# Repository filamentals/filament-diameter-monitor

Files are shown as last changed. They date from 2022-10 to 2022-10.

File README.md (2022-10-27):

# Welcome to Filamentals!

### **Motivation:** 

FilaMentals is a project to develop an optical device to monitor the diameter of 3D-printer filaments that are produced by an extractor. Custom made extractors are susceptible to produce inhomogenous filaments which would not be useful for re-use in a 3D printer. So, the future aspiration of the project is to create a feedback loop between a FilaMental device and a filament extractor, such that the extractor parameters are automatically adjusted based on the FilaMental output and the desired filament diameter is achieved.  

### **Project Description:**

 A Raspberry Pi NoIR Camera (V2) is controlled by a Raspberry Pi 3 to monitor the filament. The camera and the filament are attached to a 3D-printed casing. The casing also involves a hole for a LED, which illuminates the filament. Later, the images of the filament are analyzed with the help of [OpenCV](https://opencv.org/) package to calculate the thickness. 

### **Build Status:** 

Currently, the project is at a prototpye phase. Data can be collected from filaments, although it cannot be attached to a extruder yet. The code is being optimized to execute faster and provide a better user interface.

### **Prototype image:**

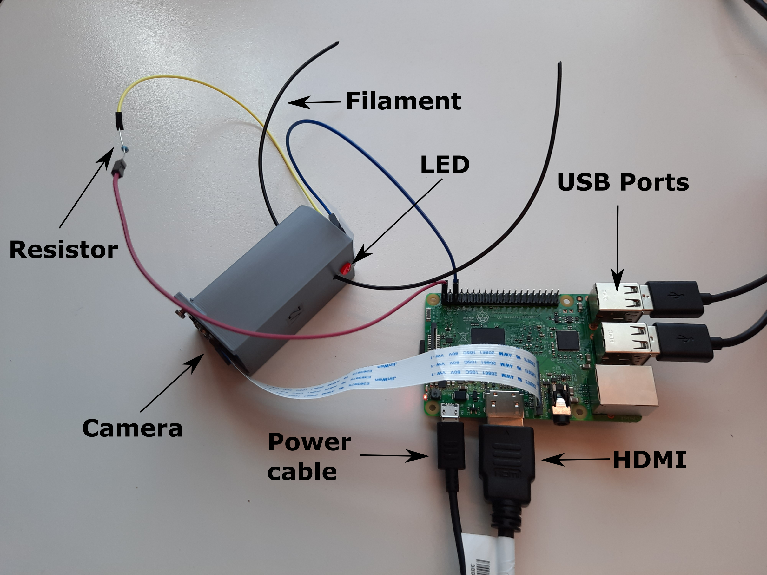
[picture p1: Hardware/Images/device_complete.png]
complete_device


The device has two parts: RaspberryPi (RasPi) and the imaging module. The former operates the device, while the latter contains the camera, filament hole, an LED and a resistor.

### **Installation:** 

For instructions to how to assemble the device click [here](Documentation/instructions/Installation.md).

### **Measurements:**

Currently this project gives live read-outs of filaments up to 5 mm of thickness. 

### **How to use:**

For the instructions of how to run the device click [here](Documentation/instructions/measurement_instructions.md)

### **Developers:**
     Ana Martins: @anaismartins
     Yoldas Cinemre: @YoldasCinemre
     Zach Meredith: @meredizp

### **License:**
For the license see [here](LICENSE).

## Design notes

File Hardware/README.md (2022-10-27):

In the *Hardware* folder the user will find these subfolders:
# Subfolders

1. [images](projects\Filamentals_Ana_Yoldas_Zach\Hardware\images) : photos about the hardware used
2. [stl_files](projects\Filamentals_Ana_Yoldas_Zach\Hardware\stl_files) : 3D models of the housing

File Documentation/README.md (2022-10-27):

In the *Documentation* folder the user will find subfolders and files:
# Subfolders

1. [feedback](projects\Filamentals_Ana_Yoldas_Zach\Documentation\feedback) : peer evaluations and feedback
2. [general_documentation](projects\Filamentals_Ana_Yoldas_Zach\Documentation\general_documentation) : contains logbook and timetable
3. [instructions](projects\Filamentals_Ana_Yoldas_Zach\Documentation\instructions) : contains installation and measurement instructions
4. [presentation](projects\Filamentals_Ana_Yoldas_Zach\Documentation\presentation) : contains pitch documentation and presentations given
5. [previous_pictures](projects\Filamentals_Ana_Yoldas_Zach\Documentation\previous_pictures) : contains photos taken by our prototype

# Files
1. [project_canvas](projects\Filamentals_Ana_Yoldas_Zach\Documentation\project_canvas_Ana_Yoldas_Zach.md) : our purpose, outcomes, and process

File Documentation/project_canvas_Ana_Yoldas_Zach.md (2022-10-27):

*Utrecht Experiment Design 2022*

# Project canvas

### POP

+ **Purpose**: to make the project requirements, boundaries, and goals as concrete as possible  
+ **Outcome(s)**: list your project steps, the best possible outcome, and the minimum desired outcome  
+ **Process**: self-reflection and discussion with your mentors

PROJECT NAME: Filamentals

TEAM: Ana Martins, Yoldaş Cinemre, Zach Meredith

# Project description  
Our main goal is to create a monitoring system for a filament extruder.
We wanted to start by following an Open Source project that consists of an optical sensor that measures the width of plastic filament in real time. From there, assuming we have the time, we want to extend to monitor other parameters, like density or extrusion rate.

*25/09/2022 Update*
- We are no longer following the open source project that uses the optical sensor, since the sensor array used in the project is no longer manufacuted.
- As a result we are now creating a method of optical measurement through the combination of a Raspberry Pi and a Pi Camera.
- The new method will need a redesinged camera mount and a way to attach the sensor to the extruder.
- We plan on using OpenCV algorithm for diamater detection of the filament.

### Open Hardware and its purpose
We started by looking at this project: https://www.sciencedirect.com/science/article/pii/S2468067218300208, which is the full filament extruder, and then looking closely at what they use for monitoring, we want to follow this open source project: https://www.thingiverse.com/thing:454584
We connect with the idea of recycling plastic and giving it a new life. Especially considering the current popularity of 3D printing, one of our ideas is to recycle failed prints or unused prints, so as to not generate so much waste.

### Potential users of the hardware and its added value
While producing the filament, it is important to know its properties, to make sure it is of high enough quality.
The potential users are the general public, since 3D printing is now so widespread. This will allow people to produce their own filament at a low cost value, while also recycling.
This can also be used for high end level prototyping, when considering extrusion rate and a time involved in 3D printing.

### Underlying physics and working principles
The first sensor we are planning on using is an optical sensor. From there, mainly thermodynamics will be involved.
The sensor directly monitors the filament being extruded and displays it in real-time.

### Required components and planned alteration to the reported recipe

*Required Components*:
- Raspberry Pi
- Pi Camera
- 3D Printed Casing
- OpenCV

Something we want to add is displaying a graph with the history of the monitored data, so that we can figure out the optimal set up for extruding. Comparing our filament with industry-produced would also be a goal.

### Chosen method of interfacing with a computer
Using a RaspberryPi, we want to create a feedback loop, where the system controlls itself when parameters are outside the acceptable values, and through this we will be able to start and stop the monitoring.

### Planned measurements
Diameter, moisture content, density, extrusion rate, elasticity, temperature.

## Mid-course review of your project state (fill this mid-course)
### Current status (24/10/22):
+ **Hardware:** Currently we have designs for 3D-printed casings that create a suitable environment for the imaging of filaments. The [installation](instructions/Installation.md) is shown to be easy, as tested by an independent group of users who had no prior experience with the set-up.
+ **Software:** We have a code that analyzes an image of the filament in the casing, and calculate the average thickness. The principles of how this works can be found [here](../Software/working_principles_summary.md).
+ **Interfacing:** The user can interact with the device by connecting the RaspberryPi to a monitor and running the code to access a graphical user interface. This interface contains a live readout of the measured diameter, as well as means to start, stop, calibrate the device. The output is then recorded in a seperate text file. Instructions to make measurements can be found [here](instructions/measurement_instructions.md).

### Deviations from the original plan:
+ We decided to restrict our measurements to filament diameters, as opposed to the initial plan to measure temperature, density, extrusion rate etc. Such goals are not within the capabilities of our current equipments and would require seperate designs of their own. We do not have the time to work on this in the timeframe allocated to the project.
+ Given the time restrictions, it is also improbable that we will manage to connect the device to a filament extruder and establish a feedback circuit. The next step for any future work on the project would be on this aspect. 

### Planned adjustments:
+ Currently, the device is not as robust as we want it to be. It seems that little changes in the positioning of filaments may cause the device to fail in making measurements. We aim to increase robustness by adding a diffuser in our design, so that the light will be more uniform. We think that this will make it easier for the device to recognize the edges of filaments.

### Updated Projects Description:
*(As written in the main README)*

FilaMentals is a project to develop an optical device to monitor the diameter of 3D-printer filaments that are produced by an extractor. Custom made extractors are susceptible to produce inhomogenous filaments which would not be useful for re-use in a 3D printer. So, the future aspiration of the project is to create a feedback loop between a FilaMental device and a filament extractor, such that the extractor parameters are automatically adjusted based on the FilaMental output and the desired filament diameter is achieved.  

 A Raspberry Pi NoIR Camera (V2) is controlled by a Raspberry Pi 3 to monitor the filament. The camera and the filament are attached to a 3D-printed casing. The casing also involves a hole for a LED, which illuminates the filament. Later, the images of the filament are analyzed with the help of [OpenCV](https://opencv.org/) package to calculate the thickness. 

## Final review of the project accomplishments (fill at the end of the course)

+ list the achievements of your project  
+ write down your plans for improving your project or making it more widely accessible

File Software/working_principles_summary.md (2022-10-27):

Here is a brief explanation of how the algorithm to analyze the images works.

First the camera takes a picture:
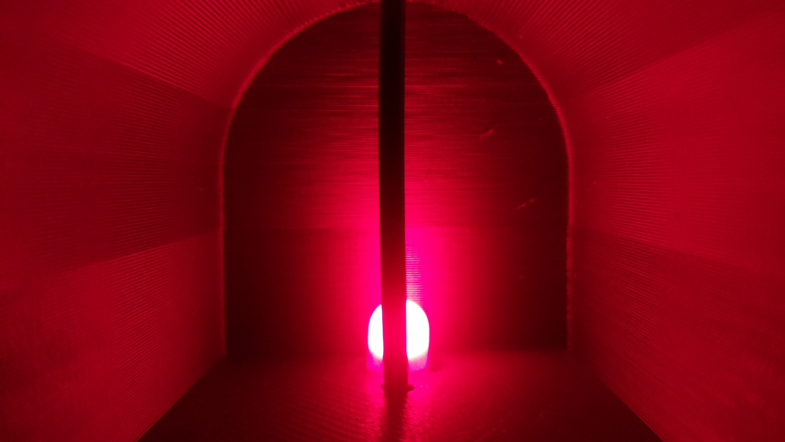
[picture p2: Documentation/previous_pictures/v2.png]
first_pic


Then it is cropped in the middle for analysis. This needed to ensure that the diameter is mostly consistent throughout the image and that it does not see the visual noise from the set-up: 

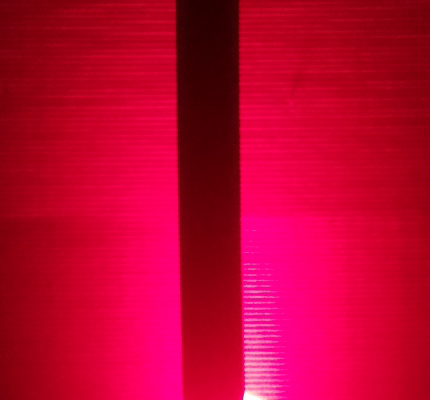
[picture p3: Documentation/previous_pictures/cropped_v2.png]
cropped


Later the code detects the edges in the image (see [here](code/edge_detection.py) for the code):

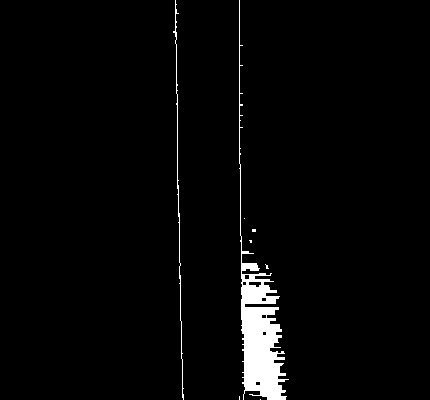
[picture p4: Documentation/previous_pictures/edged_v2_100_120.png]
edges


Then the edges of the filament are recognized as lines with the `HoughLines()` method (see [here](code/line_detection.py)). The code later seperates the image in the middle to classify the pixels belonging to each lines. Hence, it is important that the filament sits symmetrically in the middle of the image. Superimposed on the original image we can see the recognized lines (shown in blue):

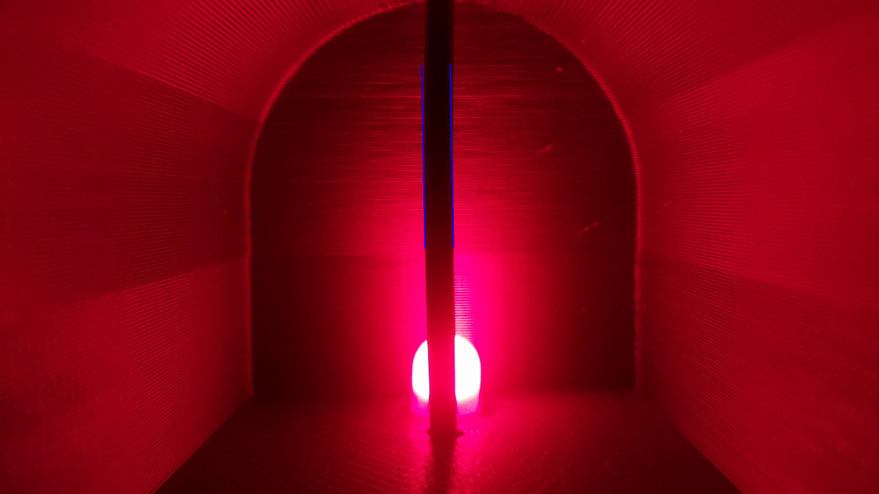
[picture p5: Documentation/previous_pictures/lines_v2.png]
lines


Finally the thickness is [calculated](code/distance_calculator.py) by taking the distance between points on the lines and averaging them. The final results are then exhibited on the interface.

**Note:** The code for the edge detection is tuned for the spesific brightness provided by the LED in the current design. If the equipment is altered, so should the code. By changing the `min_threshold` and `max_threshold` values in the [code](code/main.py), the user should find the optimal value for their set up such that the majority of the noise is filtered out and the filament edges can be detected.

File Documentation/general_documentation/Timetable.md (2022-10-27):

# FilaMental's Timetable 

**Preface**: For scheduling we are using an [online calendar](https://calendar.google.com/calendar/embed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) to plan and keep track of free time slots of the group.

## Week of September 25th:
- [X] Update Raspberry Pi OS
- [X] Connect PiCamera
- [X] Collect first image
- [X] Determine lens range
- [X] Decide if we'll use current camera case
  - Won't use the current one --> need to make a new one due to the fact that camera should be covered from external light. See [logbook](LogBook.md#300922-friday-first-use-of-opencv).
- [X] Get familiar with Python and OpenCV

 ## Week of October 2nd:
- [X] Design base for stabilizing the filament
- [X] Design method of attachment to either a printer or extruder
- [X] Test run with OpenCV in factory produced filament (known diameter)
- [ ] Update README.md with documentation for using the experiment

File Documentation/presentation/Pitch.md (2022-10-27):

# Pitch #
## Video Idea 1
1. [ ] Plastic in water
2. [ ] Pick up plastic
3. [ ] Cut to Filamentals Logo
4. [ ] Proto Lab
5. [ ] Using extruder and it's protblems
6. [ ] Goal of our project
7. [ ] Our prototypes and community involvement
8. [ ] Future of the project

## Video Idea 2
1. [X] Someone drinking from a bottle
2. [ ] Throws bottle away but slaps out of hand and put in shreeeeder
3. [ ] Cut to Filamentals Logo
4. [ ] Close up of Extruder
5. [ ] Close up of housing
6. [ ] Our growth plans (video of us working on project)
7. [ ] Reaching out to community

## Pitch narration
It is no secret that our world is drowning in plastic. These products that made our lives easy have long been unchecked. But no more! If we have the power to create plastic, we also have the power to re-shape it!

Since the dawn of time, humanity had the unresistible urge to shape the world around them. They built their civilization with the skills to mould materials, but in the process left the mother nature in peril. But no more! For if humanity can bend even the hardest metal to their will, they have the power to shape the destiny of their plastic trash. 

In the recent years, people have developed ways to re-use plastic. By putting them through steel and fire in an extruder, we can now reshape plastic in the form of filaments to be used in 3D-printers or other utilitarian purposes. However, unsupervised power yields no prosperity but only chaos. FilaMentals is a open-hardware project to create a low-cost monitoring system for the diameter of these filaments. Using a Raspberry Pi, camera, an LED and a 3D-printed casing, a FilaMental device gives a live reading of the filament diameter. The simplicity of the design allows it to be used in any custom made filament extruder. 

The future is bright, but it's surely brighter with FilaMentals in it. Our outlook involves establishing a feedback loop with the filament extruder, allowing automatic control of the machine to make filaments with thicknesses desired by the user. Thanks to this ease of use, we hope more people will be motivated to start extruding themselves and help with the global effort to battle plastic waste!

**Outro:** FilaMentals! "insert motto"

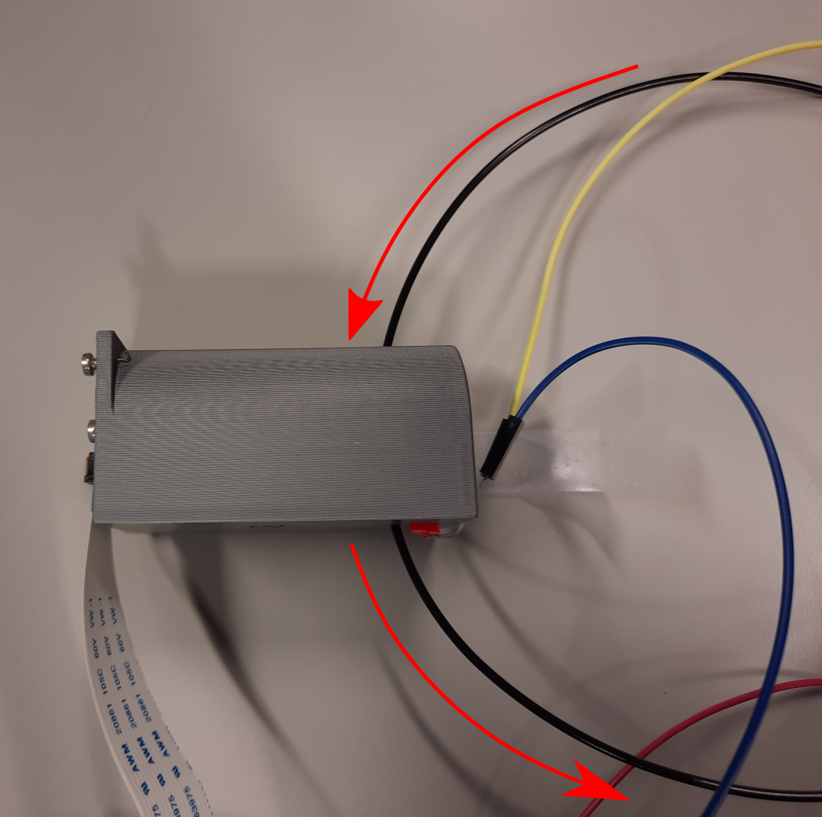
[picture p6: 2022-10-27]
Hardware/Images/filament_insertion.png

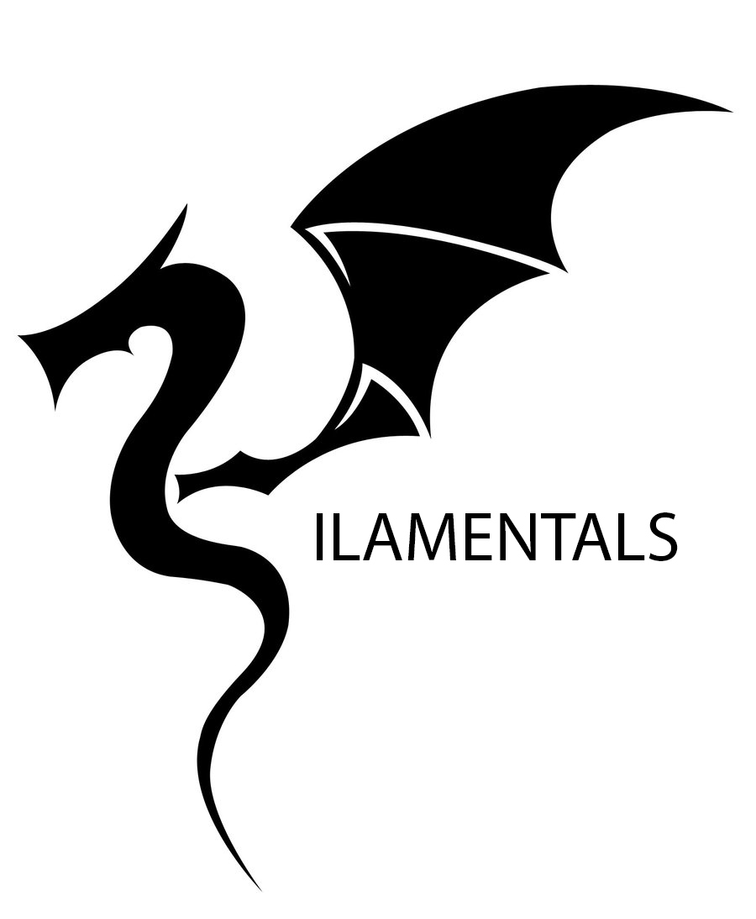
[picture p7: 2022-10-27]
Documentation/presentation/Filamentals v1.png

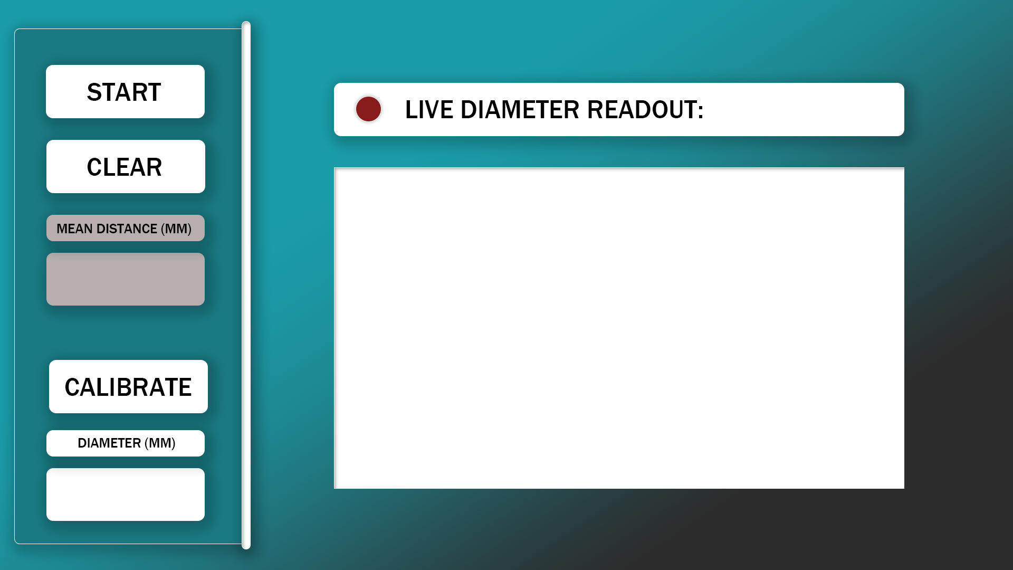
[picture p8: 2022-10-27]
Software/gui_mockup/FilaMentals_GUI.png

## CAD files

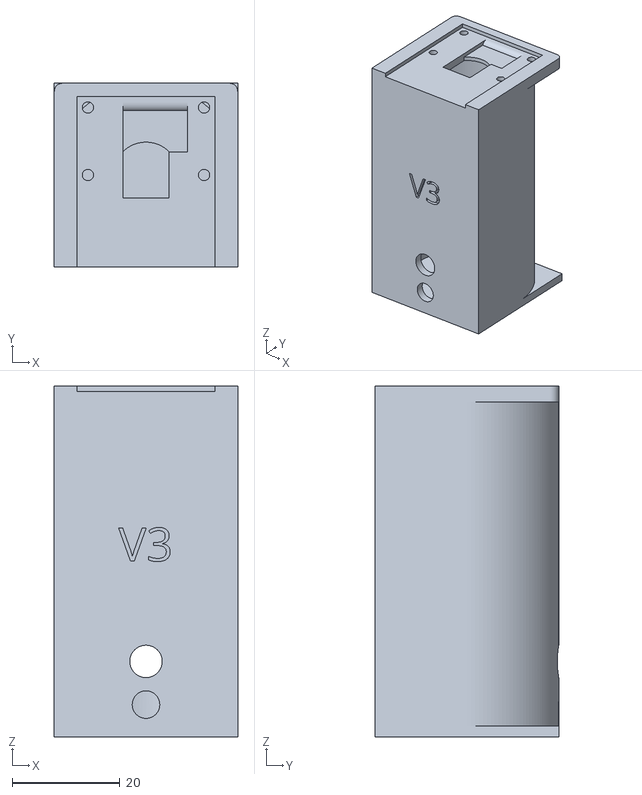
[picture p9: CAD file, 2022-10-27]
Hardware/stl_files/filament_observer_v3_chamfer.stl
34.0 x 34.0 x 65.0

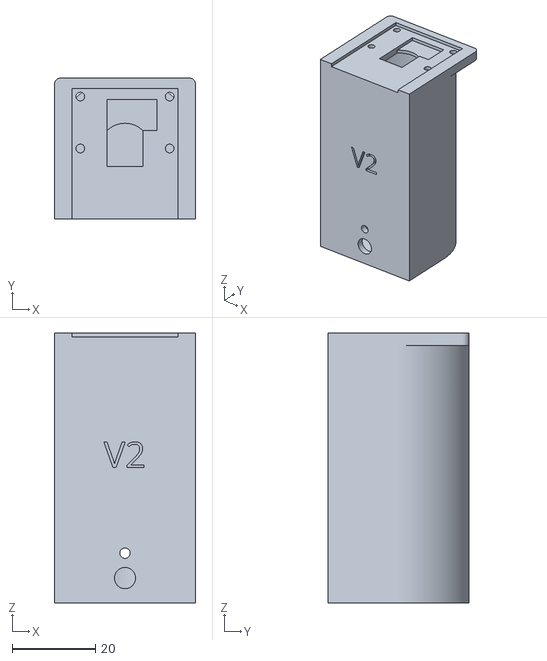
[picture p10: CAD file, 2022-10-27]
Hardware/stl_files/filament_observer_v2.stl
34.0 x 34.0 x 65.0

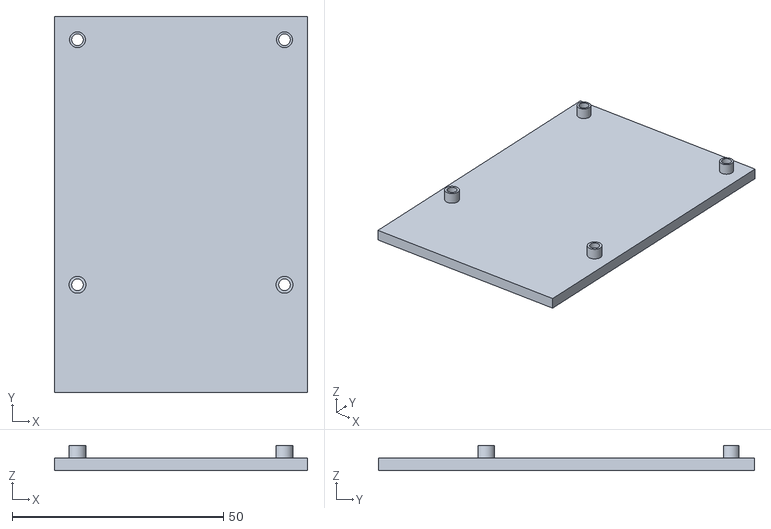
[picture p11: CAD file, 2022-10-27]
Hardware/stl_files/rpi_base_v1.stl
60.0 x 89.0 x 6.00

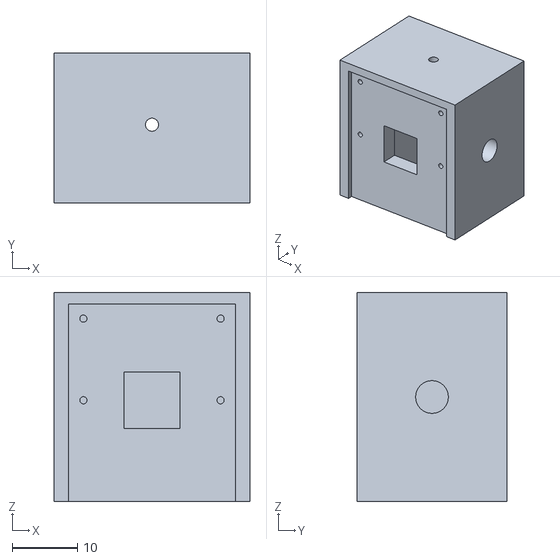
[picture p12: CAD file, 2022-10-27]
Hardware/stl_files/filament_observer_v1_LED.stl
30.0 x 23.0 x 32.0

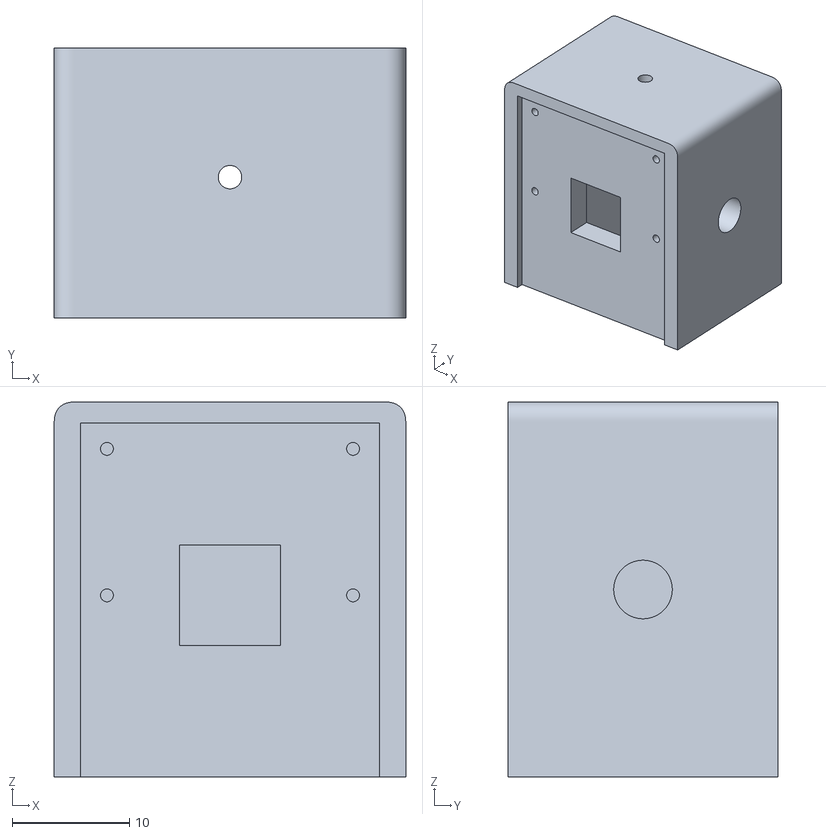
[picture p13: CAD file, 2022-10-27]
Hardware/stl_files/filament_observer_v1_LED_chamfer.stl
30.0 x 23.0 x 32.0

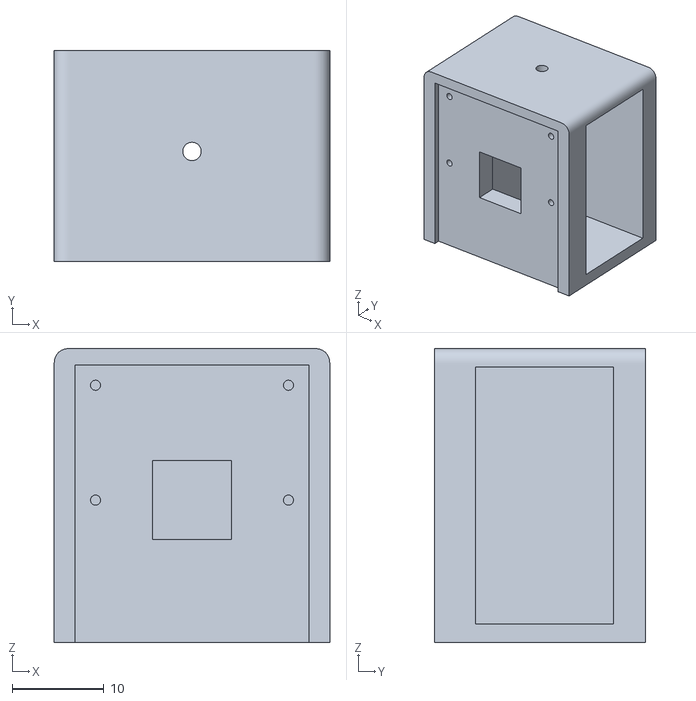
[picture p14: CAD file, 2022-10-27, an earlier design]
Hardware/stl_files/filament_observer_v1.stl
30.0 x 23.0 x 32.0

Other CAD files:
Hardware/stl_files/filament_observer_v2_chamfer.stl

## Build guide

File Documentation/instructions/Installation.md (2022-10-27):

# **Assembling the Device** 
## **Parts list:**
+ [Raspberry Pi 3 Model B](https://www.raspberrypi.com/products/raspberry-pi-3-model-b/)
+ [Raspbery Pi NoIR Camera V2](https://www.raspberrypi.com/products/pi-noir-camera-v2/)
+ Red LED, 5 mm diameter
+ Resistor, 150 Ohm
+ Female-female cables (x3)
+ [3D-printed casing](../../Hardware/stl_files/filament_observer_v2_chamfer.stl).
+ [3D-printed Raspberry Pi mount](../Hardware/SLT_Files/RPi%20Base%20V1.stl) (optional to mount on Raspberry Pi)
+ HDMI cable
+ Ethernet cable
+ Keyboard, mouse, and monitor (for interfacing)
+ USB-micro cable (power supply)
+ M2.5 mm screws (x4)
+ M2.6 mm screws (x4)(optional to mount on Raspberry Pi)

## **Hardware Assembly:** 
+ Take the M2.5 mm screws and mount the camera on to the 3D-printed casing
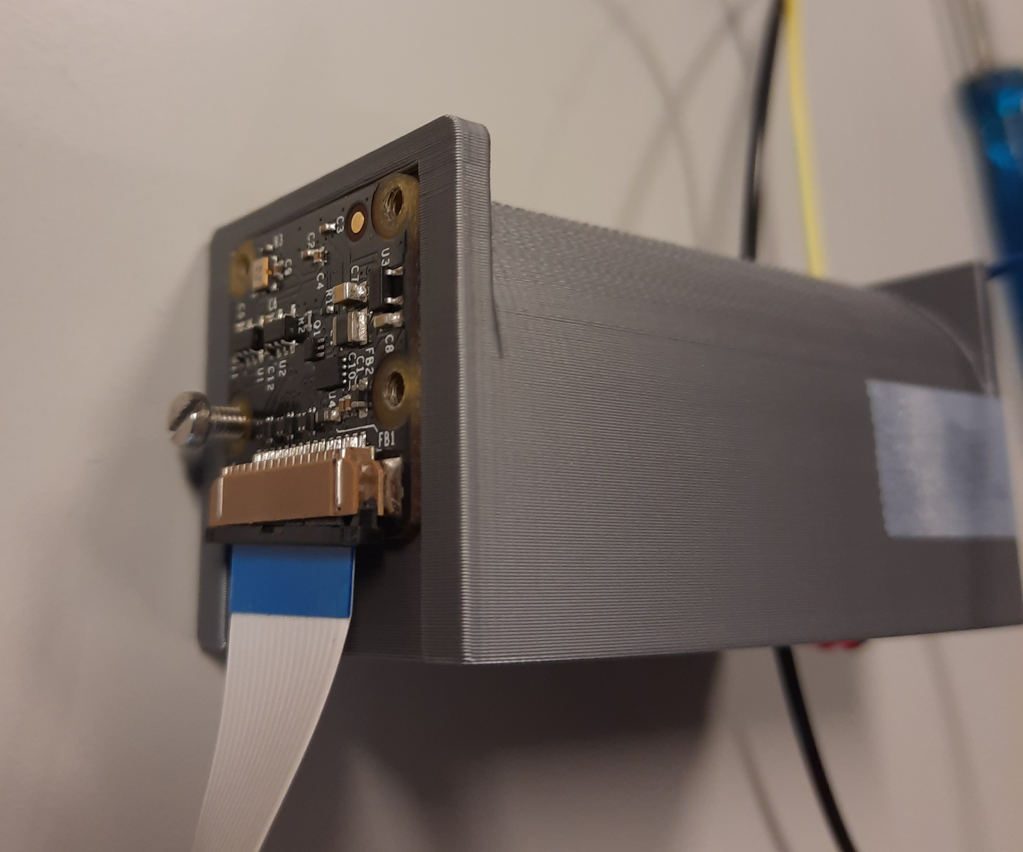
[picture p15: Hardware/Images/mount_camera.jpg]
camera_mount
  + 
+ [Connect the camera into the Raspberry Pi](https://www.techcoil.com/blog/connect-raspberry-pi-camera-module-raspberry-pi-2-raspberry-pi-3/). :warning: If you connect it while the RaspberryPi is running, the camera will break down. **Always make sure that the camera is connected to the RasPi before powering it**. :warning:
+ Connect the LED and the resistor via a female-female cable (make sure you use the longer leg of the LED). Then connect the other legs of the resistor and the LED to the Raspberry Pi as shown below:

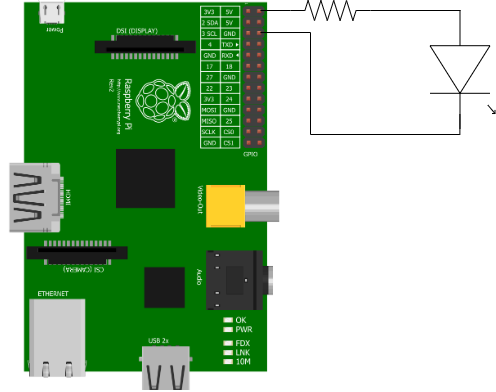
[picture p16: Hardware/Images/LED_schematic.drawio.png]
wirig_diagram
  
  **Note:** The LED and the resistor determine the brightness inside the 3D-printed casing. It is important to use the exact materials since the software is tuned accordingly. If you wish to use different materials, you would need to change some parameters in the code for it to recognize the filament. See the [summary of working principles](../../Software/working_principles_summary.md) for more information. 
+ Insert the LED in the 5 mm hole of the 3D-printed casing. 
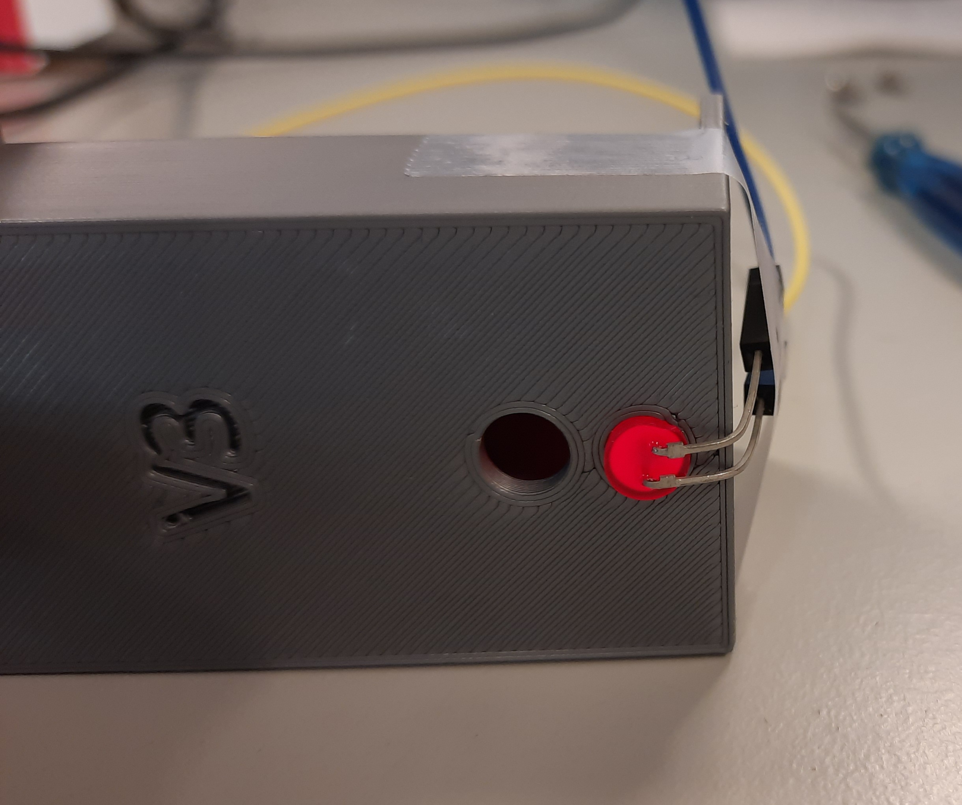
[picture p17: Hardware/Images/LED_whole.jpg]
LED_insert
  + 
+ Connect the Raspberry Pi to: 
  + the mouse and keyboard through USB ports,
  + the monitor with an HDMI cable,
  + the internet through an ethernet cable.  
  
  See the overview [image](../README.md) again, if you wish to check where the ports are on the Raspberry Pi.
+ :warning: Make sure again that the camera is connected to the Raspberry Pi :warning:.
+ Connect the power cord to the RaspberryPi. You will see a red light at the corner of the RasPi, indicating that it is powered on. The LED should also turn on at this point, if it is set up properly.

## **Software Installation:**

Once you manage to access and control the RaspberryPi through the monitor, you should follow these steps to install the required software into the RaspberryPi. If you have already done this, locate [here](measurement_instructions.md) to find the instructions to make measurements.

+ [Install the operating system](https://raspberrytips.com/install-raspbian-raspberry-pi/)
+ [Initialize the camera](https://projects.raspberrypi.org/en/projects/getting-started-with-picamera)
+ Check that the camera is connected by running the command:
  + `vcgencmd get_camera` 
  + This should give the output:
  + `supported = 1, connected = 1` 
+ Install `git` by running the commands
  + `sudo apt-get update`
  + `sudo apt-get install git`
+ Check if Python is installed by running the command
  + `python --version`
+ The version used in this project is 3.9.2. If you do not have is installed, [install it](https://handtoolsforfun.com/how-to-install-python-3-on-a-raspberry-pi-3/).
+ Clone the project repository with `git clone https://git.science.uu.nl/ued2022/ued2022.git`
+ Locate to the folder by using `cd ../ued2022/projects/Filamentals_Ana_Yoldas_Zach/Software/code` and run the command  `pip install -r requirements.txt` to install the libraries required for the code. 

**Next:** The system is ready to insert the filament and [make measurements](measurement_instructions.md!

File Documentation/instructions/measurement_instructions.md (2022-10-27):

# **Making measurements:**

The filament you wish to measure should be pushed through the two holes on the 3D-printed casing. It is most probable that the filament will be curved because of its elastic properties. To make the device work correctly, position the filament as shown below. 

filament_insertion

This will ensure that the filament sits symmetrically in the middle of the images. To understand why this is required, see the [summary of working principles](../../Software/working_principles_summary.md) of the code. 

Since the casing is a prototype and not designed to be attached a filament extruder, you will need to move the filament by hand.

Now, locate to the code folder in the project repository using: 

`cd Desktop/ued2020/projects/Filamentals_Ana_Yoldas_Zach/Software/code`

and run:

`python gui.py`

A graph will appear with the y-axis showing the thickness measurements while the x-axis shows the timesteps. You can also see the  buttons to start/stop, calibrate, and clear measurements.

## How to calibrate 
The device has a default calibration using an industrial 3D-printer filament with a diameter of 1.75 mm. However, it can be calibrated with another filament. To do that:

1. Insert a filament in the 3D-casing whose diameter you know.
2. Run the program, and let it run for at least 10 cycles. 
3. Insert the real diameter of the filament on the top right and click on "Calibrate".
4. Now you are ready to measure other filaments.

## Test measurement
Now let us make a measurement to check that the calibration is done well.

1. Insert the piece of calibration filament by paying attention to its curvature as instructed before. 
2. Start the program. The measurements will begin immediately, but you can stop and start it any time with the buttons.
3. After each measurement that appears in the graph, pull the filament slightly by hand to analyze a different segment.
4. The interface should calculate 1.75 mm for the thickness. Congratulations! The calibration is confirmed.
5. Now the device is ready to be used with other filaments.
## Possible errors
+ The terminal might show `Edges not found`. This indicates that the code failed to recognize the filament edges and/or distinguish them. When this happens, the measurement is ignored and it's not registered in the interfacial graph. **Possible Solutions:**
  + Adjust the filament as instructed above such that it's positioned symmetrically in the middle of the image (see [here](../Software/WorkingPrinciples_summary.md) to read more about why it is important.) 
  + It might also be that the filament is deformed in that region. Pull the filament a little bit to measure a different segment.
  + If the problem persists, investigate the edge detection seen by the camera. The symmetry and uniformity of the filament can be visualized here. This can be done by locating the stored photos taken by the camera. These photos can be found under [Software > output](../software/output/) and are labeled by their set min/max threshold. Select the file with the current threshold values. The current version is:
    + Min Threshold: 100
    + Max Threshold: 120
  
     *Thus the file name is as follows: edged_pic_100_120.png*
## Notes
+ For a summary of the working principles of the algorithm see [here](../Software/WorkingPrinciples_summary.md)

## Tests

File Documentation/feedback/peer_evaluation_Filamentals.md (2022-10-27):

# Reproducibility report

## Experiment/team: 
Filamentals by Ana Martins (@1760068), Yoldas Cinemre (@64795611) and Zach Meredith (@1069713)

## Reviewers: 
Riya Banerjee (@5073014) and Carlo van Maaren (@6835791)

## Report 

### Documentation:

1. **Could you understand the purpose of the experiment? Explain.**  
> Yes, this was very clear from the start as the README file in the main directory runs you through the motivation for the project and the project description.

2. **Were the safety instructions clear?**
> There were warning messages for the code and the setup (e.g. having to make sure that the camera is connected to the RaspberryPi before powering it), as well as a “Possible errors” section, but there was no true safety instructions which in our opinion also is not truly required since the project is very safe.

3. **Was the starting point and the expected duration of the measurements clear in the documentation?**  
> The starting point was easy to find because the main README file contained links to the documents in which the setup, calibration and measurement instructions were explained. The duration of the actual measurement or an estimate thereof, however, was not documented, but the GUI conveniently shows when the program settles to a particular filament diameter. For the calibration, it is said to run the program for 10 cycles, however we feel the number of cycles is not clearly indicated (the x-label of the graph in the GUI is labeled "timesteps").

4. **Does the documentation contain all necessary information to successfully reproduce the measurement? If not, what was missing?**
> We think the documentation mostly contains all the necessary information, perhaps having some extra README files in each subfolder would be helpful to better navigate through the project. 

5. **Did you get stuck at some point? What extra help did you need to proceed?**
> Initially, we got stuck trying to install all the required programs on our laptops which resulted in a few bugs we had to resolve (i.e. “from main import main errors” and having some problems installing picamera on Windows). After discussing with the project team, we figured out that we could simply use the desktop that was already connected to the device and from there everything went smoothly.

6. **Are you encouraged to reproduce previous measurements? How easily could you navigate through the project documentation?**
> The measurements we reproduced were the calibration and test measurement, after which we tried the extruded filament and a few cables to test the device. The calibration and test measurement were well-explained and we were encouraged to actually perform them in the documentation. 
Navigating through the project documentation was clear, but we do have a few pointers which will be given below (7).

7. **What can be improved in the documentation?**
> We like the use of the PIP install via the requirements file, but it is only described in the installation file. It would be useful if this was also mentioned in the software folder. For our purposes, however, it was fine since we did not have to install anything ourselves. 
To continue, the gui.py file is now located in the code folder (within the software folder) but there is also a “gui” folder in which there are only an image and a psd-file of the graphical user interface. We could imagine that people would look into the gui folder for the Python code as well, so perhaps renaming that folder to “GUI_images” or something similar would be better. You could also [convert your Python program to an executable file](https://www.geeksforgeeks.org/convert-python-script-to-exe-file/) and place that in the folder (while also having the actual code in the “code” folder). 
In addition, we would advise you to make the “Documentation” folder more structured by the use of subfolders, similar to those in the hard- and software folders.
Finally, as stated, we would use README files in the subfolders as well so that the reader is guided better through your documentation. This would also resolve some of the improvements mentioned above.

**On the scale of 1-5 (1: top quality, 5: disappointing) how do you assess the documentation? Please justify your grade based on the questions above.**

#### Documentation grade: <mark>**2**</mark>

### Measurements:

1. **Can you operate the setup with the provided instructions?**
> Once we figured out that we had to connect the power cable and use the desktop that was already connected, operating the setup was rather easy because of the graphical user interface. The provided instructions were clear and sufficient, but – as mentioned in the documentation – the software returned “Edges not found” a lot, especially when using the extruded filament. We will go more into some ideas we have  to resolve this in the following.

2. **How close were the results you obtain to the previously reported results?** 
> The calibration and test measurements were spot on. The measurements we performed after that were also pretty close (± 0.1 mm).

3. **Is the analysis procedure easy to understand? Summarize it briefly in your own words.**
> The analysis is done by the software itself. Its function is described in a working principles summary which was a very nice addition. This procedure we now want to describe in our own words.
The camera makes an image of the interior of the device in which the filament is placed. Behind the filament there is a LED which illuminates the interior of the chamber, so that the camera can capture the silhouette of the filament. This image is then cropped so that the variation in filament diameter will not influence the analysis. After that, you use a set of OpenCV functions to find the edges of the filament cross section (`cv2.canny`). Next, you use the `Houghlines()` method from OpenCV to recognize the edges as lines and compute the distance between the two. This should then give the diameter of the filament. 

4. **Is the setup robust and safe to operate?** 
> Yes, it mostly is. We would suggest making a holder for the RaspberryPi and all the electronics since they seem somewhat fragile.

5. **Did you encounter any issues? Could you troubleshoot those issues without contacting the owners?**  
> Once we have figured that we had to use the desktop that was already connected to the RaspberryPi, we only encountered issues in the form of the “Edges not found” warning which, as stated, was already mentioned in the documentation. Sometimes by adjusting the filament (which is something you also give as a possible solution), the warning went away, but most of time this was not the case. After discussing with a member of the project team we came to the conclusion that we should just accept this for the current standing of the project.

6. **What part of the measurement procedure did you appreciate most?**  
> We think the GUI is a very nice touch as this makes the experience for the user a lot nicer. Though not technically part of the measurement, we would also like to comment that getting an insight into the working principles of the algorithm was also a highlight of the reproducibility exercise.

**On the scale of 1-5 (1: top quality, 5: disappointing) how do you assess the measurements reproducibility? Please justify your grade based on the questions above.**

#### Reproducibility grade: <mark>**1.5**</mark>

### Interactions:

1. **If you had to perform work on this part of the project, would you have selected the same goal or aimed at something else? Please, explain.**  
> Initially we thought that you were going to actually build a full filament extruder from which we personally would not have immediately thought of making a filament sensor. After the presentation it became clear that there was already a filament extruder in Lili’s Proto Lab. From here, it indeed seems logical to look into improving this device instead and a filament sensor is a step we also could have taken from there. 

2. **Which instructions did you need from the owners on top of the written files?**  
> As beforementioned, the only thing we really needed was the pointer that we had to work on the desktop that was already connected to the device. We were initially starting to download the required libraries and trying to get the code working, but in the end all of that was already done for us! Thank you, team Filamentals!

3. **Does the experiment accomplish its stated purpose?**
> It does. We were able to determine the diameter of several filaments and wires. 

4. **What do you recommend to the project owners to improve their complete package?**

> _Documentation_

We think most of the project documentation is clearly ordered and complete. That being said, we do have a few tips (some of which are already discussed above):
1.	Add README files to the subfolders as well. This way you know where to find what in the subfolder. For example, when we looked for the gui.py file, we initially were looking in the “gui” folder, assuming the graphical user interface might be located in a separate folder. Something to add here, is that you could look into converting the GUI to an executable file and only place that file in the “gui” folder while keeping the actual code in the “code” folder ([conversion instructions](https://www.geeksforgeeks.org/convert-python-script-to-exe-file/)).
2.	Installing the required libraries via a single PIP install (through the requirements file) is a very good addition. For now it is only described in the installation file, however. We think it would be useful if this was also mentioned in the software folder. 
3.	We would advise you to make the “Documentation” folder more structured by the use of subfolders, similar to those in the hard- and software folders.

> _Measurements_

The measurements were very easy to perform because of the graphical interface. This is really nicely done! The graph shown in the GUI had a x-label “timesteps”. We wondered whether those actually refer to the number of cycles or an actual measure of time. In the former case, we would advise you to alter the calibration instructions so that they match. Otherwise, in the latter case, we would advise you to also include the number of cycles / elements that were used for the averaging so that you do not have to keep track of that yourself. You could also inform the user that the calibration (and with that the 10 cycles) are done.

> _Hardware (bonus)_

Since you guys did so well in the documentation and measurement side of the project, we also wanted to include some ideas we had on fixing some of the issues that you are still trying to solve (e.g. hopefully get rid of the “Edges not found” warnings). 
1.	To start, we noticed that the LED results in a flair in the images which in turn causes the OpenCV modules to recognize different edges than the ones of the actual filament. This could maybe be resolved by using a dim (homogeneous) back light which covers the entire back wall (i.e. the wall which is captured by the camera), or by making a ‘hallway’ for the LED (to reduce difference in radial distance from the light source) and using a diffusive plastic sheet (to dim the LED – might not be necessary anymore after including the hallway). This way the entire background will be illuminated in the same manner and contrast will be improved. In the images we clearly see the print lines which result in unwanted analysis results. By removing the back wall and replacing it with something non-3D printed (i.e. the back light), these lines will no longer be present and the OpenCV detection will most likely function a lot better. Furthermore, due to the light being a lot dimmer, the flairs should not be there anymore. If you manage to find a multi-color back light, you will also be able to adjust the color to have maximum contrast with the filament. 
2.	To tie in on this, we would also suggest painting the side walls of the chamber in black so that more of the indirect light is absorbed. This way the filament will only be illuminated from the back and print lines in the side walls will not cause lines in the images which could be recognized by the OpenCV modules. 
3.	Furthermore, you could look into using adjustable rollers on either side of the filament entrance and exit holes as this would make the feeding a lot more consistent, with less bending of the filament. By making them adjustable you are still able to use different filament gauges.
4.	As stated, we would also like to suggest making an enclosure for the wiring to improve the robustness of the device.
5.	In some talks we had about your project, you mentioned that you were also in the process of speeding-up the code. We think you will find a way to do this, but we also want to give you a different option that involves more of the hardware side. We encountered [this YouTube video]( https://www.youtube.com/watch?v=RYgdLPe_T0c) which describes a cheap solutions that requires much less computational power and analysis. Perhaps you can combine the two mechanisms and write an algorithm that uses the pre-estimated diameter to more quickly find the filament diameter through the optical path.
6.	Finally, we came across [this article](https://www.researchgate.net/publication/346555509_Open_Source_3-D_Filament_Diameter_Sensor_for_Recycling_Winding_and_Additive_Manufacturing_Machines) in which a multi-axes measurement is described using mirrors. This would give you a better indication of the actual shape of the filament, thereby making it a much better sensor than the 1D alternatives. If you guys have time, it would be awesome if you could also implement this!   

______

### Response to reviewers

_This part must be filled by the project owners based on the peer feedback_

1. **Which major adjustments did you make based on this feedback?**
 1. [ ] We are planning to redesign our lighting system to try to elimintate the "no edge found" error.
- [X] Design a diffuser slot
- [X] Design more reflective (homogenous) background
 2. [X] We plan on changing the x-label in our live graph from timesteps to cycles.
 3. [ ] We will design a more robust housing and consider the touch screen for the Raspberry Pi.
 4. [ ] We will further explain the calibration principle to clarify future confusion.
 5. [X] We will output the diameter of the filament
 6. [X] We will implement a red = recording
 7. [ ] We will upload our project details to JOGL.
 8. [ ] We will write down our clear goals, how far we plan to get, and the following steps of our project.
 9. [X] Update project canvas.
 10. [ ] We will clarify that the Raspbery Pi is a desktop and only needs a monitor and keyboard to use, not a separate laptop.
 11. [ ] We will clarify the link why making diameter measurements correlates to recycling plastic.
 12. [ ] We will try and record information aobut how long each measurement takes.
 13. [ ] We will look into the theoretical background of this project.
 14. [ ] We will clean up and reorganize our subfolders to adapt to the knowledge of each individual user.
- [X] Rename image folder to GUI images
- [X] More sub-folders in Documentation
- [X] README in each sub-folder with description of that sub-folder

2. **Do you agree with the graded assessment of the reviewer?**
In the context of this course, our team believes that our documentation is clear and precise enough to be considered a 1.5 over the 2 that we were originally scored.

**On the scale of 1-5 (1: really helpful, 5: disappointing) how do you assess the peer evaluation? Please explain.**
1.5: We believe that the feedback given was very descriptiive and near a perfect response. We were given, not just the problems of our project, but also possible solutions to overcome these problems. The only negative we found was that some of the advice was a little unhelpful simply due to them not being possible for integration to rasberry pi. Feedback is good, only when it applies to the project.

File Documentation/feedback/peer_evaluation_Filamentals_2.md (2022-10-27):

# Reproducibility report

## Experiment/team: 
[Filamentals](projects/Filamentals_Ana_Yoldas_Zach) by Ana Martins (@1760068), Yoldas Cinemre (@64795611) and Zach Meredith (@1069713)

## Reviewers: 
Uma Lau (@5127416)

## Report 

### Documentation:

1. **Could you understand the purpose of the experiment? Explain.
> In the part of Open Hardware and its purpose, there are links for people to look in detail of the background for the project and the used open hardware, which is desirable. However, I do think it would be better if there are more explanations of project purpose or a summarized description. The contents about the experiment purpose in both README and project canvas is a bit sketchy for now, which merely mention the custom-made extractors are insusceptible to produce a re-useable homogeneous filament in 3D printer. Indeed, this allows me to know the reason of building a monitoring system for filament extruder; whereas, without introducing why extractors fail to produce such a filament, how the extractors work and look like, and etc., it would be hard for me to obtain a deeper understanding of how much the monitoring system improve the facility. Also, there seems have a jump in the explanation of the aim, for instances, I am a bit confused on how this device aid to the recycling of the failed prints or unused prints. Doing measurements are not filling the gap of that.     

2. **Were the safety instructions clear? 
> Yes, the safety instructions are clear. There are warning symbols around the bolded safety remarks, which are placed in the right place and with appropriate amount.

3. **Was the starting point and the expected duration of the measurements clear in the documentation?  
> Despite the duration of the measurements is not shown, there is clear and readable instruction on performing the measurement. I can follow them easily. 

4. **Does the documentation contain all necessary information to successfully reproduce the measurement? If not, what was missing? 
> I found it is a bit difficult to push the material into the casing. During this process, the material is damaged a little bit and it is also stuck in the halfway. If this will affect the measurement result in some way (because the diameter might be slightly different) or disturbing the imaging (because there might be some crumbs left inside the casing after various measurements), I think this should be mentioned in the documentation.     

5. **Did you get stuck at some point? What extra help did you need to proceed?
> Everything is stated and labelled, that is good! I can follow every step on the hardware building. The steps for software installation are also listed in a good order with useful links and grey highlights. The code is not that difficult to comprehend.       

6. **Are you encouraged to reproduce previous measurements? How easily could you navigate through the project documentation?  
> Yes, there is not much error sources for the results of the measurement. If you can follow every step listed in the page and take care of the possible (procedural) errors, the results are quite stable. Meanwhile, the project documentation navigation is managed very well because each step is clearly stated. Both hardware and software components used are quite handy to construct. 

7. **What can be improved in the documentation?  
> Still, I hope there will be more explanations in the part of [working principles] ( projects/Filamentals_Ana_Yoldas_Zach/Software/WorkingPrinciples_summary.md) or the theoretical background. Also, if the pictures are adjusted in a smaller size and with some descriptions below, that would be nicer.   

On the scale of 1-5 (1: top quality, 5: disappointing) how do you assess the documentation? Please justify your grade based on the questions above.

#### Documentation grade: <mark>**2**</mark>

### Measurements:

1. **Can you operate the setup with the provided instructions? 
> Yes. Thanks for the labelling, that’s helpful and handy. 

2. **How close were the results you obtain to the previously reported results? 
> The resolution and shape of material edge obtained is quite like the provided results. Probably there is few millimeter’s differences, but that is omittable and within the acceptable range.  

3. **Is the analysis procedure easy to understand? Summarize it briefly in your own words.  
> All analysis of the measurement is done in the computer program. The graphical interface can calculate the thickness for us. We only need to compare the results. It is easy to handle.  

4. **Is the setup robust and safe to operate? 
> Yes, the setup is robust and safe and the caution about the power is also stated clearly. One thing is the thickness of material seems not fit the hole of the casing very well, maybe it is good to either make the hole larger or produce the thickness of material smaller.   

5. **Did you encounter any issues? Could you troubleshoot those issues without contacting the owners?
> No, everything is done smoothly. For troubleshooting, there is enough help from the part of possible errors.

6. **What part of the measurement procedure did you appreciate most?  
> I appreciate the part of test measurement; they are clear and simple.  

On the scale of 1-5 (1: top quality, 5: disappointing) how do you assess the measurements reproducibility? Please justify your grade based on the questions above.

#### Reproducibility grade: <mark>**1.5**</mark>

### Interactions:

1. **If you had to perform work on this part of the project, would you have selected the same goal or aimed at something else? Please, explain. 
> As mentioned above, I am not fully understanding the purpose of this project. I also think the measurement on the thickness is the main thing of this device, but if I could realize in a deeper way of its function, I would probably aim on other things.   

2. **Which instructions did you need from the owners on top of the written files?  
> The written files are well and sufficient.

3. **Does the experiment accomplish its stated purpose? 
> Yes, its measure the thickness as expected.

4. **What do you recommend to the project owners to improve their complete package?  
> I think add a README files to every subfolders would be better. Another thing is I feel the measurement maybe a bit simple. I recommend adding more type of measurements. 

______

### Response to reviewers

_This part must be filled by the project owners based on the peer feedback_

1. Which major adjustments did you make based on this feedback?  
2. Do you agree with the graded assessment of the reviewer?  

On the scale of 1-5 (1: really helpful, 5: disappointing) how do you assess the peer evaluation? Please explain.

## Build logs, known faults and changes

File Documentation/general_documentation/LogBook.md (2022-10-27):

# Welcome to the LogBook of our progress

Here the user can find notes on each step taken in the development of the project.

## 26/09/2022, Monday
+ Initial attempt to make pi camera work. 
+ :warning: DO NOT turn on RaspberryPi before attaching the camera. Always plug everything out, attach the camera and then plug the cords in to turn on RasPi. Otherwise, you will blow the camera. :warning:

## 29/09/2022, Thursday
### Instructions on how to connect the pi camera and taking a picture
+ Plug the camera in the RasPi. 
  + (instructions on how to open the holder, put the cord in and locking it, maybe with pictures)
+ Plug all the other necessary components to turn on RasPi. These are:
    + Mouse and keyboard
    +  Monitor
    +  Powercord
    +  **Note**: When the camera is attached, it takes the RasPi longer to turn on. If it takes too long, plug out the power and put it in again.
 +  You will see the screen of the RasPi on the monitor. Using the icon on the top, open a terminal. 
    + Use the command: `vcgencmd get_camera` to check that the camera is connected. If it is, you will get the output: `supported = 1, connected = 1`.
    + To take a picture use the command: `raspstill -o ~/Desktop/image.jpg`
    + **Note:** If the camera is out of focus, you can gently move the camera lens (counter-) clockwise to adjust the focus. 

## 30/09/22, Friday, First use of OpenCV
Yesterday the [first image](first-pic.jpg) was taken. The goal of this session is to use OpenCV to analyze the image and get a measure of the filament's thickness. Following sources are to be studied and used:
+ [Ordering coordinates clockwise with Python and OpenCV](https://pyimagesearch.com/2016/03/21/ordering-coordinates-clockwise-with-python-and-opencv/)
+ [Measuring size of objects in an image with OpenCV](https://pyimagesearch.com/2016/03/28/measuring-size-of-objects-in-an-image-with-opencv/)

Using the [code](../Software/code/edge_detection.py) to detect the edges of the filament we get [this](../Software/output/edged_first.png) kind of images. **Notes on the image:**
+ It seems that the lightning of the image is important for edge detection. It can be seen that the bright section on the top of the filament is detected as two lines. We need to avoid bright reflections off the surface of the filament. 
  + **Proposed solution**: We should aim to make a casing covering the camera, with a fixed light illuminating the sample. This would eliminate the light source as a random variable, increasing the reproducability. 
  + [ ] **Task**: Think about and ask for a small light source that might work for this purpose. Can the red LEDs we have would be useful?  

## 01/10/22, Saturday
**Today's goals**:
+ [ ] Achieving recognition of the top and bottom lines of the filament by the code
+ [ ] Figuring out the required distance between the filament and the camera such that the edges of it is not blurred.
+ [ ] Installing OpenCV in RasPi.
  + Apparently Python 10.2 crashed our OS... Reinstalling for next time. 
+ [X] Delving more into the tools of OpenCV.
  + It seems that the method used [here](https://pyimagesearch.com/2016/03/28/measuring-size-of-objects-in-an-image-with-opencv/) might not be applicable in our case, because that code requires the complete object to be in the image. It works by recognizing the object, drawing a rectangular contour around it and then taking the corners. In our images the filament will span across the whole image, hence the code might not recognize it as one object.  

## 02/10/2022 Sunday
**Today's goals**
+ [X] Reinstalling Pi OS (try the newest version since we knew that the camera was the issue the first time)
+ [X] Reinstall Python on Pi
  + We actually ended up leaving the Python that already came with Bullseye (Python 3.9) in fear of breaking it again. If there's any conflicts between our computers and the Pi, we'll downgrade in our computers. 
+ [X] Reinstall OpenCV
  + It worked first time...
+ [X] Reinstall GIT to simplify the process by coding on our computers
  + Already had the latest version installed! I can see the appeal in this new OS...
+ [X] Preliminary Camera Module Housing

## 03/10/22, Monday
+ [X] Go to the protolab and print the preliminary camera housing.
  + [This design](../Hardware/SLT_Files/FilamentObserver_w_LED_and_Chamfer_V1.stl) is being printed. 
+ [X] Get RGB LED
  + No need for it, red LED works pretty well already.
+ [X] Screw everything in the casing and take a picture
  + The picture is taken under the name pic_v1 
+ [X] Use edge detection software in the image
  + It seems that putting the light source at the side causes bright spots on one side, leading to a bad recognition of the edge on that side. 
  + **Proposed solution**: Put the light source at the side of one of the filament holes.
    + We did that by drilling a hole and the processing of the image leads to [this](../previous_pictures/edged_v140_100.png)
    + Now we get more clear lines detectable by eyes. Next step is to make it so that the computer also recognizes them as lines. 
  + New method to detect lines: [Houghline](https://www.geeksforgeeks.org/line-detection-python-opencv-houghline-method/)

## 07/10/22, Friday
**Summary of the progress since monday**:
+ We designed and printed V2 of the casing this time with a longer distance between the camera and the filament
  + Requires us to crop the image to analyze only the region around the middle of the filament, thus reducing unwanted edges that are recognized due to illumination of the sorrounding area.
  + Tried a white LED but it is too bright, causing unwanted edge detection --> stick to the red LED.
+ The [algorithm](../Software/code/edge_detection.py) to detect the edges of the filament as lines and measure the average distance (in pixels) between them works. 
  + There is variation however between initial measurements. We could see different measurements in pixels of the same, industrial filament
+ **Shortcomings for now**
  + In order to categorize which of the recognized lines belong to which edge of the filament, the code seperates the image in the middle. This poses a problem if the filament is positioned in such a way that it's curved. Then the code fails.
  + **Possible solutions:**
    + Design a casing such that the filament is strecthed, thus reducing the curvature.
    + Instruct the user to position the filament accordingly. 
  
### Progress today
+ Ana created the first version of the interface
  + Does temporal measurements (in pixels) and records them in a graph 
+ Yoldaş wrote more on the README
  + The skeleton seems to be ready to instruct the user to make a first measurement
  + [X] Images of the set up needs to be added
  + [X] Extra documents need to be created for further help if the user needs such as:
    + [X] How to connect another LED and changing the analysis parameters if the user uses other LEDs or resistors
    + [X] A summary of the working principles of the code (with images)

## 08/10/22, Saturday
+ Zach designed a nice interface.
+ Yoldaş put images of the set up in README and created the instructions of how to connect the LED and summary of the working principles.
+ Ana perfected the measurements and the interface.

## 10/10/22, Monday
**Goals:**
+ [X] Make the final presentable interface.
+ [X] Go over the doumentation and instructions to finalize them.

## 17/10/22, Monday
+ [X] Respond to the feedback.

## 20/10/22, Thursday
+ [ ] Make new casing with a hole for a light diffuser.
+ [ ]

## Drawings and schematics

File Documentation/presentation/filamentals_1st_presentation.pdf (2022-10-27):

01

# FilaMentals

ANA MARTINS
YOLDAŞ CINEMRE
ZACH MEREDITH

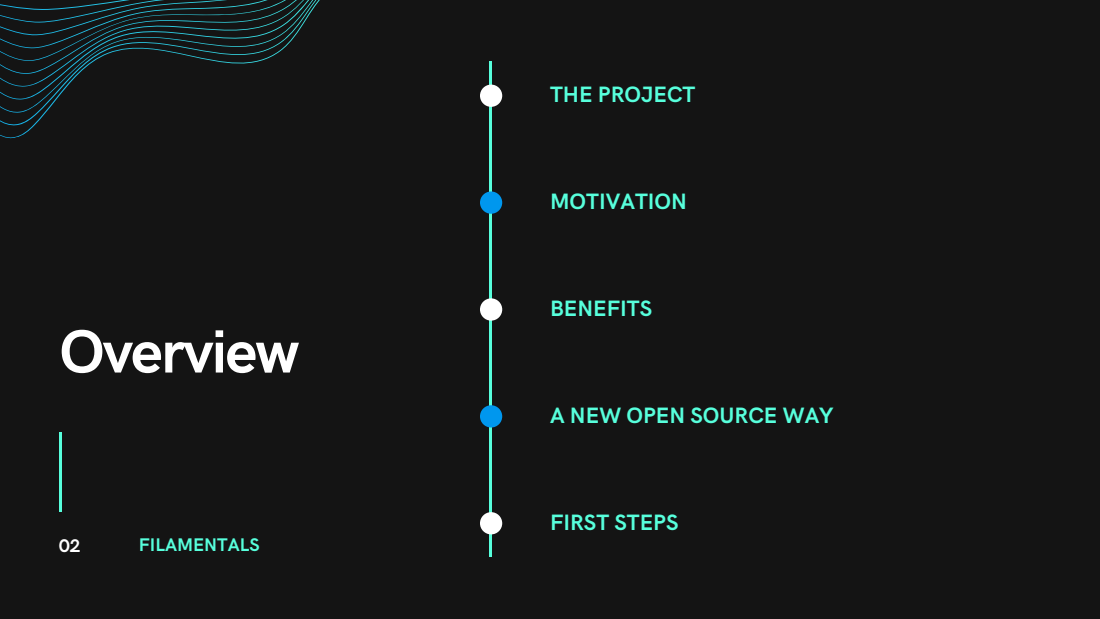
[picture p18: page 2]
Overview; THE PROJECT; MOTIVATION; BENEFITS; FIRST STEPS; 02 FILAMENTALS

A NEW OPEN SOURCE WAY

# The Project

## HOW WE GOT HERE

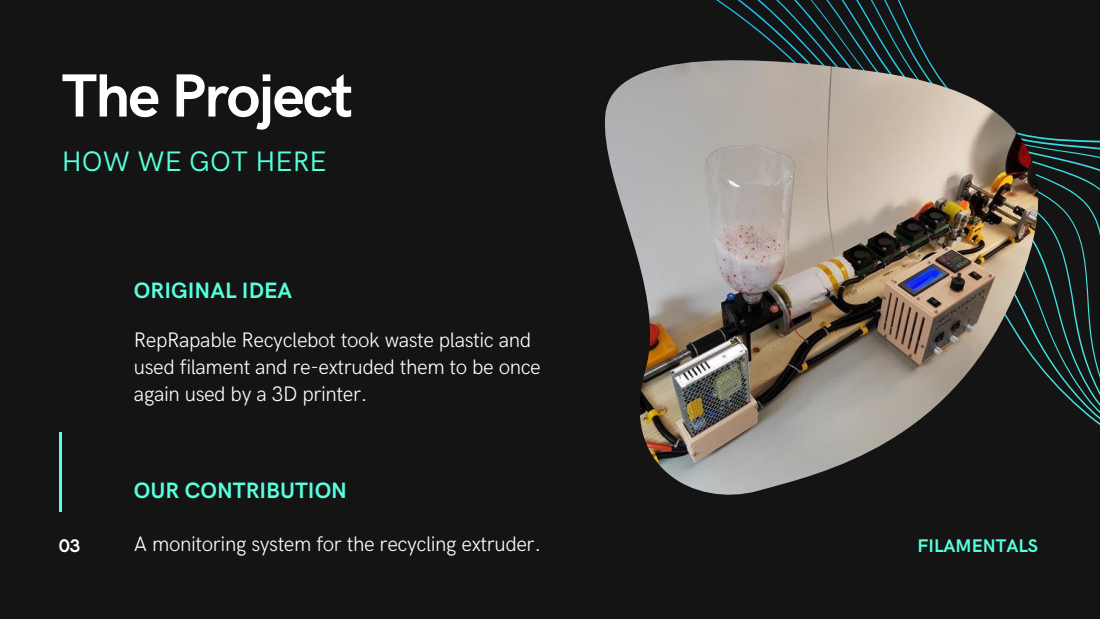
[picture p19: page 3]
ORIGINAL IDEA; OUR CONTRIBUTION; A monitoring system for the recycling extruder.; FILAMENTALS

RepRapable Recyclebot took waste plastic and
used filament and re-extruded them to be once
again used by a 3D printer.

# Motivation

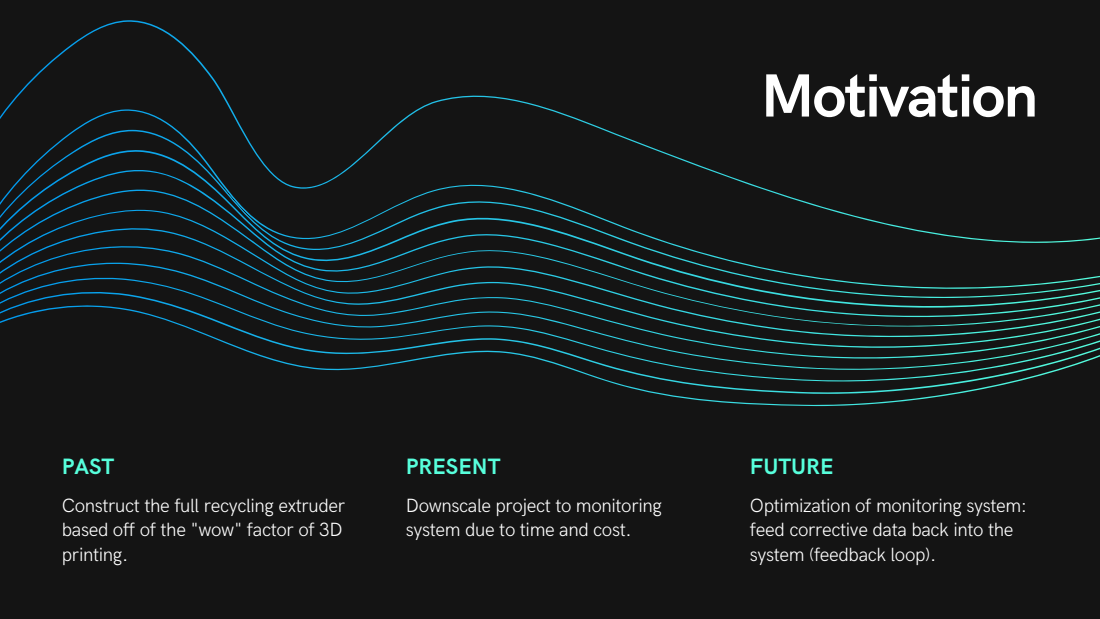
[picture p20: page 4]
wow; " factor of 3D

PAST
Construct the full recycling extruder
based off of the "
printing.

PRESENT
Downscale project to monitoring
system due to time and cost.

FUTURE
Optimization of monitoring system:
feed corrective data back into the
system (feedback loop).

# Benefits

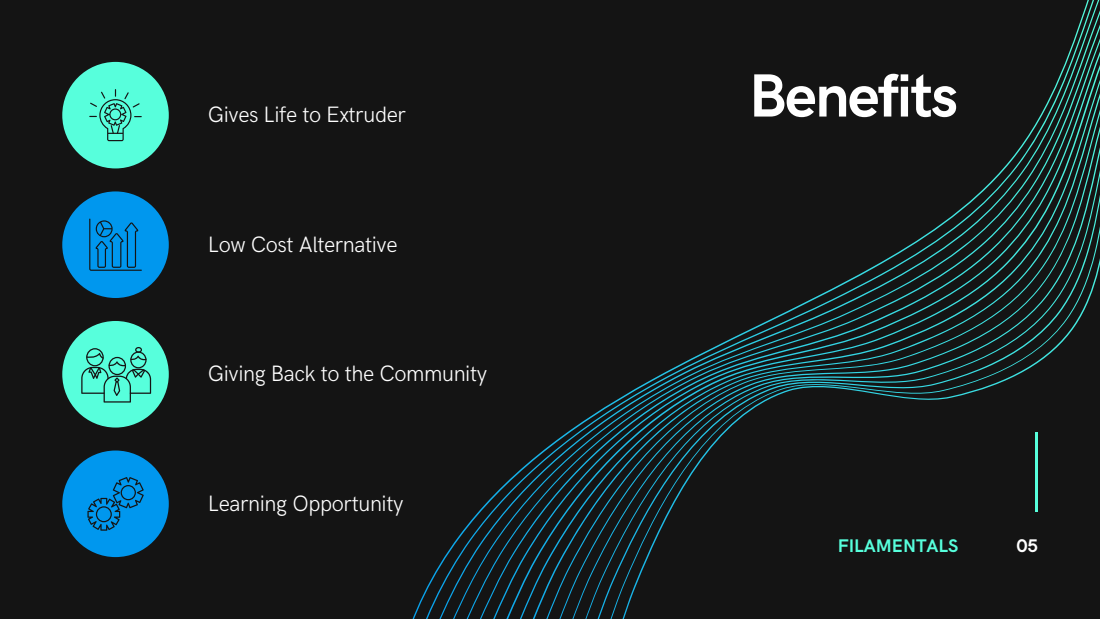
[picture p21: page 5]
FILAMENTALS; Learning Opportunity

Gives Life to Extruder

Low Cost Alternative

Giving Back to the Community

# A New Open Source Way

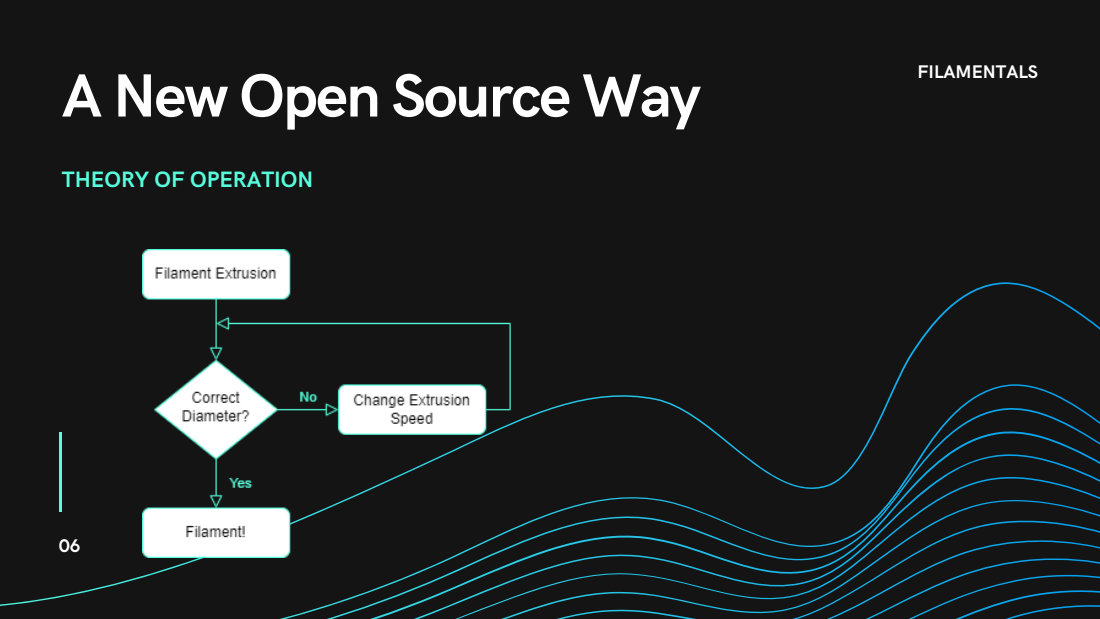
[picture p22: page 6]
FILAMENTALS

THEORY OF OPERATION

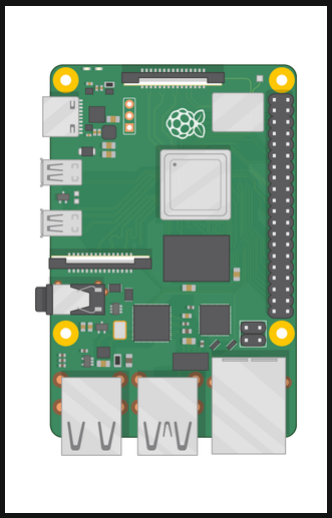
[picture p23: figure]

07

# A New Open Source Way

HARDWARE

FILAMENTALS

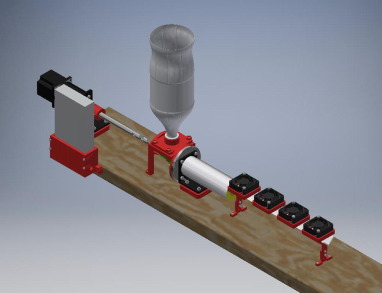
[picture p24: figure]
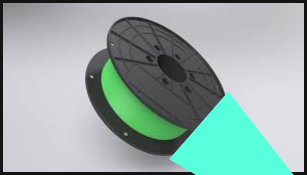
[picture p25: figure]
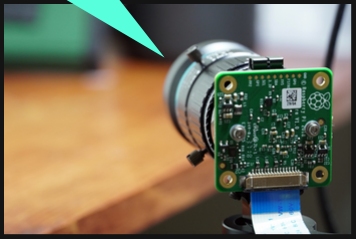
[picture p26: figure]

# A New Open Source Way

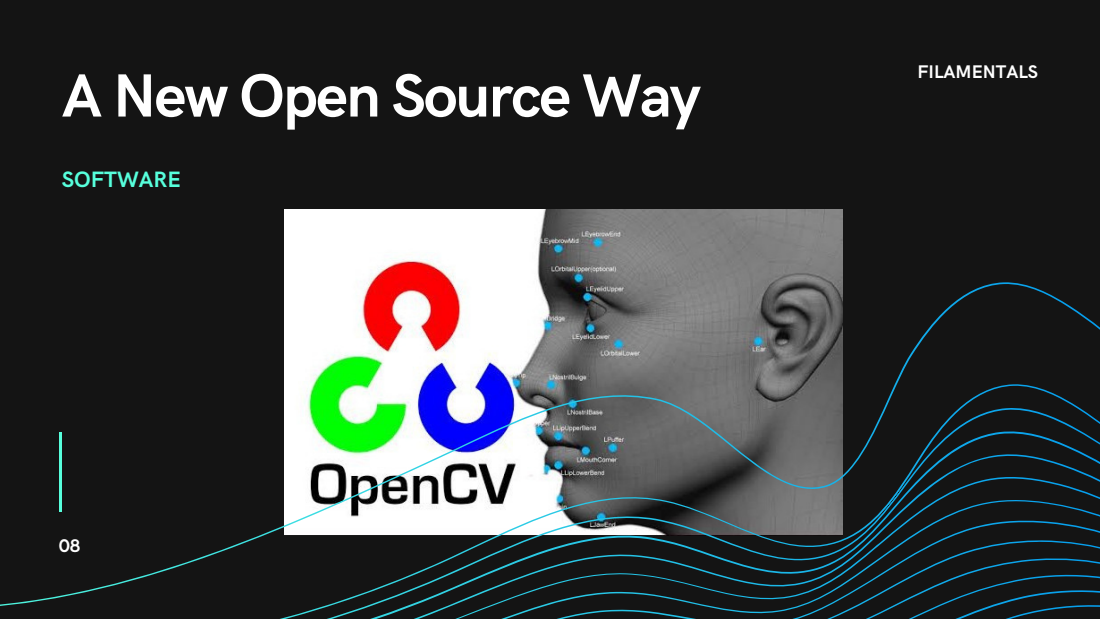
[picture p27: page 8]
SOFTWARE; FILAMENTALS

# First Steps

Testing the Extruder
Getting the Raspberry Pi working and starting on the detection algorithm Creating a 3D model for a camera mount

FILAMENTALS 09

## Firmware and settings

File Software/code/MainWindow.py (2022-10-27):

import time
from pyqtgraph.Qt import QtCore, QtGui, QtWidgets
import pyqtgraph as pg
from PyQt5.QtWidgets import QPushButton, QLabel, QLineEdit
import webbrowser
from statistics import mean
import datetime

# TODO
# change python lists into numpy arrays

from main import main


class MainWindow(
    QtWidgets.QMainWindow,
):
    def __init__(self, *args, **kwargs):
        super(MainWindow, self).__init__(*args, **kwargs)

        self.setWindowTitle("FilaMentals")

        self.setFixedWidth(1155)

        self.graphWidget = pg.PlotWidget()
        self.graphWidget.setLabel("left", "Diameter (mm)")
        self.graphWidget.setLabel("bottom", "Cycles")
        self.setCentralWidget(self.graphWidget)
        self.graphWidget.setYRange(0, 7, padding=0)

        self.filename = "../output/data-" + datetime.datetime.now().isoformat() + ".txt"
        self.file = open(self.filename, "w")

        # list of all the diameter values to calculate the mean
        self.diameter = []
        # variables for plotting
        self.x = list(range(-100, 0))  # 100 time points
        self.y = [0] * 100  # 100 data points


        # black square to put buttons
        self.mean_diameter_label = QLabel("lalala", self)
        self.mean_diameter_label.setGeometry(QtCore.QRect(0, 0, 1080, 100))
        self.mean_diameter_label.setStyleSheet("background-color: #000000")

        # filamentals button
        self.filamentals = QPushButton("FilaMentals", self)
        self.filamentals.setStyleSheet("background-color: #1a9ca8")
        self.filamentals.setGeometry(10, 10, 260, 25)
        self.filamentals.setFont(QtGui.QFont("Ariel", 10))
        self.filamentals.clicked.connect(self.filamentalsMethod)

        # start button
        self.startbutton = QPushButton("Stop", self)
        self.startbutton.setStyleSheet("background-color: #1a9ca8")
        self.startbutton.setGeometry(10, 35, 100, 25)
        self.startbutton.setFont(QtGui.QFont("Ariel", 10))
        self.startbutton.clicked.connect(self.startMethod)

        # clear button
        self.clearbutton = QPushButton("Clear", self)
        self.clearbutton.setStyleSheet("background-color: #1a9ca8")
        self.clearbutton.setGeometry(10, 60, 100, 25)
        self.clearbutton.setFont(QtGui.QFont("Ariel", 10))
        self.clearbutton.clicked.connect(self.clearMethod)

        # label saying mean diameter
        self.mean_diameter_label = QLabel("Mean Diameter (mm): ", self)
        self.mean_diameter_label.setGeometry(QtCore.QRect(120, 35, 150, 25))
        self.mean_diameter_label.setFont(QtGui.QFont("Ariel", 10))
        self.mean_diameter_label.setStyleSheet("background-color: #b7afaf")

        # value of the mean diameter
        self.mean_diameter_number_label = QLabel("0", self)
        self.mean_diameter_number_label.setGeometry(QtCore.QRect(120, 60, 150, 25))
        self.mean_diameter_number_label.setStyleSheet("background-color: #b7afaf")
        self.mean_diameter_number_label.setFont(QtGui.QFont("Ariel", 10))

        # label saying diameter
        self.real_diameter_label = QLabel("Set Reference Diameter (in mm):", self)
        self.real_diameter_label.setGeometry(QtCore.QRect(925, 10, 220, 25))
        self.real_diameter_label.setStyleSheet("background-color: #1a9ca8")
        self.real_diameter_label.setFont(QtGui.QFont("Ariel", 10))

        # edit for the real diameter
        self.real_diameter_edit = QLineEdit(self)
        self.real_diameter_edit.setText("1.75")
        self.real_diameter_edit.setValidator(QtGui.QDoubleValidator())
        self.real_diameter_edit.setGeometry(QtCore.QRect(925, 35, 220, 25))
        self.real_diameter_edit.setStyleSheet("background-color: #ffffff")
        self.real_diameter_edit.setFont(QtGui.QFont("Ariel", 10))

        # calibrate button
        self.calibrate_button = QPushButton("Calibrate", self)
        self.calibrate_button.setGeometry(QtCore.QRect(925, 60, 220, 25))
        self.calibrate_button.setStyleSheet("background-color: #1a9ca8")
        self.calibrate_button.setFont(QtGui.QFont("Ariel", 10))
        self.calibrate_button.clicked.connect(self.calibrateMethod)

        #"record" label
        self.recording = QLabel("  O", self)
        self.recording.setGeometry(QtCore.QRect(280, 10, 75, 75))
        self.recording.setStyleSheet("background-color: #1a9ca8;" "color: #FF0000")
        self.recording.setFont(QtGui.QFont("Ariel", 25))

        # label for live diameter readout
        self.current_diameter = QLabel("Live Diameter Readout: 0", self)
        self.current_diameter.setGeometry(QtCore.QRect(355, 10, 560, 75))
        self.current_diameter.setStyleSheet("background-color: #1a9ca8")
        self.current_diameter.setFont(QtGui.QFont("Ariel", 25))

        # graph
        pen = pg.mkPen(color="#1a9ca8")

        # timer
        self.data_line = self.graphWidget.plot(self.x, self.y, pen=pen)
        self.timer = QtCore.QTimer()
        self.timer.setInterval(1)
        self.timer.timeout.connect(self.update_plot_data)
        self.timer.start()

        # only for calibration purposes
        self.real_diameter = 0
        self.ratio = 1.75/65 #original ratio


    def filamentalsMethod(self):
        if self.filamentals.isEnabled():
            webbrowser.open_new_tab(
                "https://git.science.uu.nl/ued2022/ued2022/-/tree/main/projects/Filamentals_Ana_Yoldas_Zach"
            )
            print()
            print("Thanks for visiting :D")
            print()

    def startMethod(self):
        """
        method for starting and stopping the acquisition with a button
        """
        if self.startbutton.isEnabled():
            if self.startbutton.text() == "Stop":
                self.startbutton.setText("Start")
                self.timer.stop()
                self.recording.setStyleSheet("background-color: #1a9ca8;" "color: #1a9ca8")
            elif self.startbutton.text() == "Start":
                self.startbutton.setText("Stop")
                self.timer.start()
                self.recording.setStyleSheet("background-color: #1a9ca8;" "color: #FF0000")

    def clearMethod(self):
        """
        method for clearing the graph
        """
        if self.clearbutton.isEnabled():
            self.data_line.clear()
            self.diameter = []
            self.x = list(range(-100, 0))  # 100 time points
            self.y = [0] * 100
            self.file.close()
            self.filename = "../output/data-" + datetime.datetime.now().isoformat() + ".txt"
            self.file = open(self.filename, "w")

    def calibrateMethod(self):
        """
        sets the new real value for the distance and new ratio pixel/mm
        """
        if self.calibrate_button.isEnabled():
            self.real_diameter = float(self.real_diameter_edit.text())
            self.ratio = self.real_diameter / mean(self.diameter)

    def update_value(self):
        """
        update mean distance value
        """

        s = 0
        if len(self.diameter) > 0:
            self.mean_diameter_number_label.setText(
                "%.2f" % (mean(self.diameter) * self.ratio)
            )    

    def update_plot_data(self):
        """
        update data
        """

        ndiameter = main()

        if ndiameter != 0:
            self.diameter.append(ndiameter)

            self.x = self.x[1:]  # Remove the first y element.
            self.x.append(self.x[-1] + 1)
            self.y = self.y[1:]
            self.y.append(ndiameter * self.ratio)

            self.file = open(self.filename, "r")
            if not self.file.read(1):
                self.file = open(self.filename, "w")
                self.file.write(str(ndiameter * self.ratio) + "\n")
            else:
                self.file = open(self.filename, "a")
                self.file.write(str(ndiameter * self.ratio) + "\n")

            self.data_line.setData(self.x, self.y)  # Update the data.

            self.current_diameter.setText("Live Diameter Readout: %.2f" % (ndiameter * self.ratio))
        
        if (len(self.diameter) > 0):
            print("Mean of the diameter in pixels: " + str(mean(self.diameter)))
            print()

        self.update_value()

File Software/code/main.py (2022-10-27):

from camera import get_picture
from edge_detection import get_edge
from line_detection import get_lines
from distance_calculator import get_distance


def main():
    # original image from the camera

    filename = "../output/pic.png"

    time2adjust = 1

    min_threshold = 100
    max_threshold = 120

    get_picture(filename, time2adjust)
    original, edged = get_edge(filename, min_threshold, max_threshold)
    right_lines, left_lines, rightn, leftn, x0, y0, a, b = get_lines(original, edged)
    if x0 != [0]:
        distance = get_distance(right_lines, left_lines, rightn, leftn, x0, y0, a, b, original)
        return distance
    else:
        return 0
